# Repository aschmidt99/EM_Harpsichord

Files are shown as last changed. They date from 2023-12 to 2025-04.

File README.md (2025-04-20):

# NOTE: This repo is outdated!
Hello! While this repository still covers the basics of Lorentz Force Actuation and feedback, a more comprehensive and curated version can be found on this newer repository: [Sparksichord Project](https://github.com/aschmidt99/Sparksichord_NIME2025)

# Electromagnetic Harpsichord

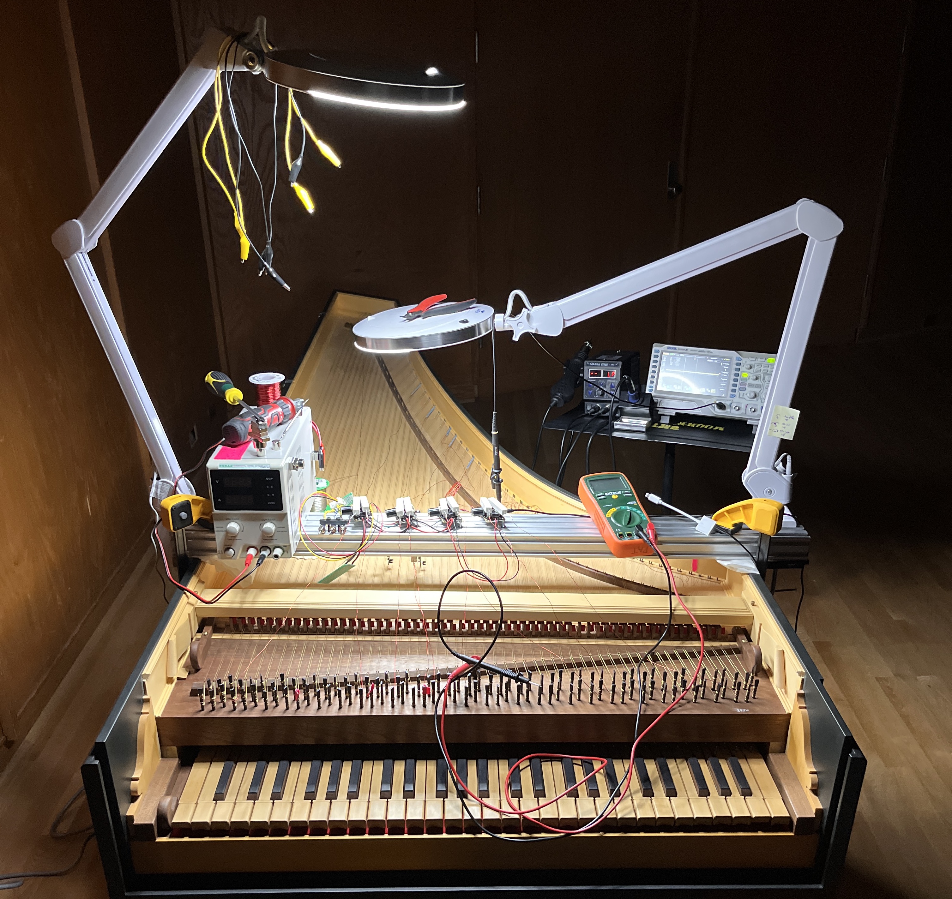
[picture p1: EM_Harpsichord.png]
EM_Harpsichord


The EM Harpsichord is an augmented harpsichord that uses optical sensors, audio power amplifier chips, and some simple signal processing to sustain the vibrations of its brass strings. This early prototype uses one circuit board for every string you wish to sustain. A work-in-progress performance/demonstration was given on October 2nd, 2023 at the 63rd Annual University of Michigan Organ Conference. For this demonstration, 3 strings had optical sustaining enabled and 8 strings had audio-playback enabled.

## Video Examples
Here is a [selection of audio examples](https://drive.google.com/drive/folders/1B2c4qz-7Rl1Y2wPH64m0Ud0_MTGL74a2?usp=sharing) of both sustainers and audio playback through the harpsichord strings.

## Working Principle
This simple board uses a ITR20403 Optical Photo-interrupt to sense the vibrations (position) of a harpsichord string. The derivative of this signal is amplified and sent to a 5-Watt audio amplifier chip (PAM8406) that is normally used to power small 4 or 8 ohm speakers. Rather than connect to a speaker, the output terminals of the speaker chip are connected to each end of one of the strings on a harpsichord. The amplified signal pushes current through the string, which generates an alternating magnetic field that interacts with a strong magnetic field from permanent neodymium magnets.

The working principle is similar to the more familiar eBow, but rather sensing and inducing vibrations with electromagnetic coils, we sense with an optical sensor and actuate with Lorentz force actuation.

## Simple System Diagram
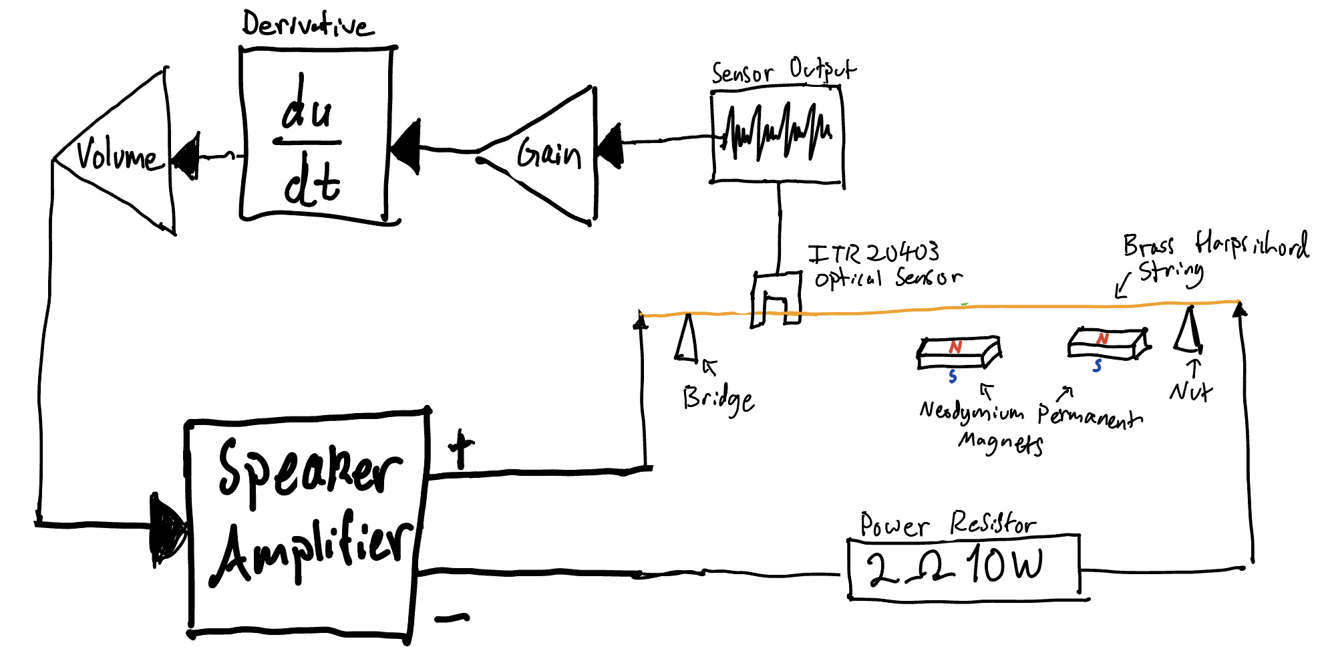
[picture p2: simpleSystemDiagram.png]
simpleSystemDiagram

This is the signal flow for the sustainer circuit in each board. You need one circuit board for each string you wish to sustain.

## The Circuit Board
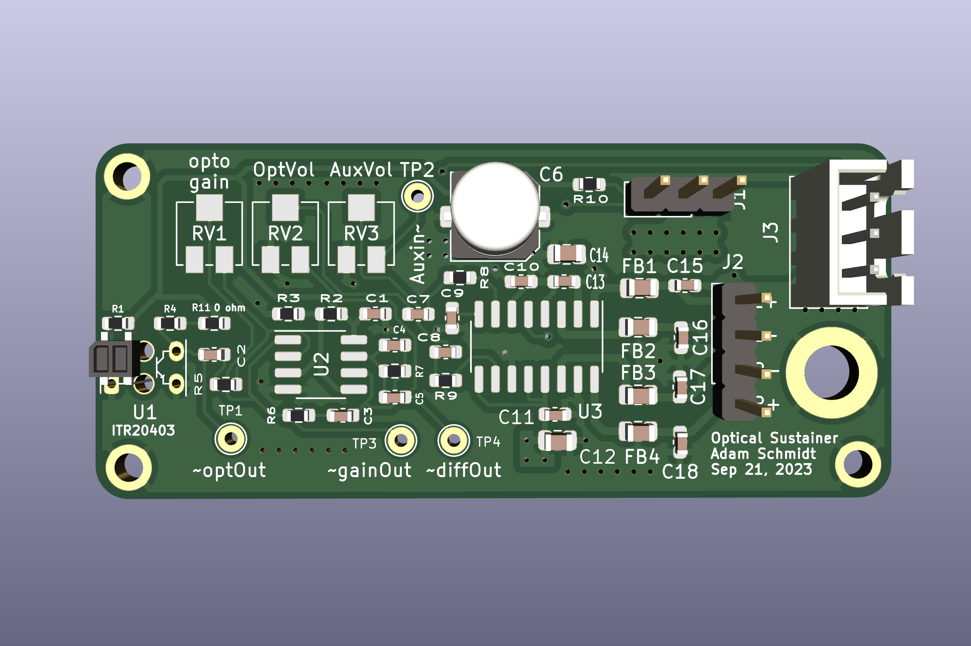
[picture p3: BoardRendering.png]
PCB

The circuitboard is thin enough to fit between the harpsichord's strings. We mounted them to an aluminum extrusion C Beam with slide nuts, M4 screws, and some small 3D printed brackets.

## How to order
### JLCPCB
If you wish to have this exact board, you can order these circuit boards from JLCPCB by uploading GERBER-EMHarpsichord_Sustainer+Playback.zip to JLCPCB. Also upload BOM-EMHarpsichord_Sustainer+Playback.csv and CPL-EMHarpsichord_Sustainer+Playback.csv to have JLCPCB assemble the board for you.
(Note: Double check the orientation of each IC in JLCPCB. They are often incorrect by default.)

### Reach out to me
Alternatively, reach out to me (schmia@umich.edu) in case I have some extra :)

### Other board house
If you are familiar with a different board house, feel free to export as you usually would from KiCad.

### Notes before ordering/assembling
If you order based on my files, the optical sensor will be placed on the wrong side of the board. I found it easier to source the components from JLCPCB and desolder/resolder the ITR20403 to the other side of the board. If you can find them for cheap elsewhere, it would probably save you a small headache to order them separately and omit them from the board when ordering.

## How to use
### Wiring up
- A 3 Pin JST XH 2.54mm connector supplies 5V, Ground, and an auxiliary audio input. If you don't anticipate using audio playback, simply wire up the 5V and Ground and you are good to go. Chain several boards together to sustain multiple notes. We put a SPST switch between each board's ground and the power supply ground to allow us to select which strings were activated individually.
- The PAM8406 chip is advertised to support 4-8 ohm loads, though the data sheet notes that it can support loads down to 2 ohms. The data sheet also notes that outputs of the PAM8406 amplifier chip have built in short circuit protection, and the outputs will not activate if they detect less than 2 ohm load. Therefore, you must ensure that there are at least 2 ohms between the (+) and (-) terminal of each speaker output.
	- Most of the brass strings on our harpsichord measured much less than 1 Ohm, so we opted to put a 2-Ohm 10W Power Resistor between each string and one of the terminals the selected channels.

### Magnets
- To induce vibration, the strings must be exposed to a strong magnetic field. We have been using N52 neodymium magnets (purchased from kjmagnetics.com) for this purpose. The strength of the vibration is proportional to the strength of the magnetic field, and although the presence of just one or two magnets usually is enough to get sound going, more magnets seems to encourage a higher acoustic output.
- The orientation of the magnet does matter. Flip the magnet back and forth to determine which side is inducing the sound you like. One side should sustain the fundamental frequency of the string and the other may damp the fundamental while favoring odd harmonics.
- If you wish to use multiple magnets on a string, you will most likely want all of their poles pointed in the same direction, although interesting magnet placement can yield interesting results...

### Channels
- The 'left' output channel of the board is connected to the optical sensor, which creates a closed feedback loop to sustain vibrations on the connected string.
- The 'right' output channel of the board amplifies an auxiliary input signal.

### Additional Notes:
- The optical sensor needs to be placed very precisely over the string to ensure it picks up the vibration. The sensing range of the string is very small and is easy to clip. You can use an oscilloscope on test point 1 (TP1) to make sure the sensor isn't clipping before the gain stage.
- If it is clipping (and you do not like the output tone), consider moving the sensor board closer to a termination point of the string where its range of vibration is much smaller. This should yield a smoother sustaining sound.
- The feedback loop is very sensitive to the position of the sensor. You will likely notice timbral changes as you change the point on the string where the sensor is located, the position of the sensor over the string, and the positions of the magnets.
- Bar magnets induce stronger vibrations than cylindrical with the same pull force.
- The resistance of a metal string is a function of its material, gauge, length, and temperature. The higher the resistance, the more apt the string is to detuning. If your strings are detuning too much, try using a thicker wire, more conductive material, or lower current. If you are building a new instrument rather than augmenting an existing one, try different string lengths.

## Design References
- the 'RelevantDocuments' folder holds data sheets and some blog/forum posts I found helpful while designing the board. (Dave Corsie's blog)[https://www.davecorsie.com/optical-pickup-blog] helped me figure out how to design the optical pickup circuit and the DIYAudio blog helped me make a better PCB layout for the PAM8406 Chip.

## Future Improvements
### Support Loads < 2 Ohms
One of the most obvious shortcomings of this system is the wasted power. If a given string is only 0.2 Ohms and we compensate with a 2 Ohm resistor, most (~90%) of the power is being dissipated as heat through the resistor rather that contributing towards generating vibrations. I suspect looking into circuits that are anticipating extremely low loads such as ribbon speaker amplifiers will be a worthwhile endeavor and likely be a solution for the next version of this circuit.

### Lower Heat Buildup
On the other hand, the large dummy load ensures the majority of the power is dissipated somewhere other than the string, which prevents heat buildup (and thus detuning) in the string. The magnetic field generated by the string is proportional to current only - it does not factor in voltage. Therefore, an alternative system improvement may be to increase string gauges to /decrease/ overall resistance and continue to utilize the power resistors.

### Controlled Detuning
With more advanced feedback control, it may be possible to control how much or little each string is detuned during actuation. This could allow the performer to change tuning systems rapidly and on-the-fly - a process that usually takes considerable time and attention.

### Sustainer on every string
A natural progression for the project is to add a sustainer board for every string so that we can sustain any strings rather than just the few we chose for our work-in-progress demonstration. A double-manual harpsichord might work well, where one manual controls the sustainers and the other moves jacks and plucks the strings as usual.

### Sensing the keys
In the next version of this project, we aim to actively sense the position of each harpsichord key to use as a control signal for the sustainer of each corresponding string. Mechanically separating the harpsichord keys from the strings will allow us to map and re-map the interaction between key presses and actuation however we wish.

## Acknowledgements
- This project was enabled by Professor Joseph Gascho, Associate Professor of Music and Director of the Stearns Collection at the University of Michigan Ann Arbor.
- This project was inspired by the (Electromagnetic Resonator Piano)[http://instrumentslab.org/research/mrp.html], a project by Andrew McPherson at the Augmented Instruments Lab.
- Additional inspiration and insight was provided by (Techniques and Circuits for Electromagnetic Instrument Actuation)[https://www.nime.org/proceedings/2012/nime2012_117.pdf] by Andrew McPherson (see Section 2.4 - Lorentz Force Sustaining).

## Software Versions used
- KiCad (6.0.7-1)-1 for MaxOS Version 13.4.1
- LTSpice 17.0.40 for OS X

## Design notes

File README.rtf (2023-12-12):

# Electromagnetic Harpsichord

The EM Harpsichord is an augmented harpsichord that uses optical sensors, audio power amplifier chips, and some simple signal processing to sustain vibrations on the brass strings of the harpsichord. This early version uses one circuit board per string you wish to sustain. A work-in-progress performance/demonstration was given on October 2th, 2023 at the 63rd Annual University of Michigan Organ Conference.

## Working Principle

This simple board uses a ITR20403 Optical Photo-interrupt to sense the vibrations (position) of a harpsichord string. The derivative of this signal is amplified and sent to a 5-Watt audio amplifier chip (PAM8406) that is normally connected to small 4 or 8 ohm speakers. Rather than connect to a speaker, the output terminals of the speaker chip are connected to each end of one of the strings on a harpsichord. The amplified signal pushes

## How to order:

You can order these circuit boards by uploading GERBER-EMHarpsichord_Sustainer+Playback.zip to JLCPCB. Additionally upload BOM-EMHarpsichord_Sustainer+Playback.csv and CPL-EMHarpsichord_Sustainer+Playback.csv to have JLCPCB assemble the board for you.
- Double check the orientation of each IC in JLCPCB. They are often incorrect by default.

Alternatively, reach out to me (schmia@umich.edu) in case I have some laying around still :)

## How to use:

### Wiring up

- The PAM8406 chip is advertised to support 4-8 ohm loads, though the data sheet notes that it can support loads down to 2 ohms. The data sheet also notes that outputs of the PAM8406 amplifier chip have built in short circuit protection, and the outputs will not activate if they detect less than 2 ohm load. Therefore, you must ensure that there are at least 2 ohms between the (+) and (-) terminal of each speaker output. Most of the brass strings on our harpsichord measured less than 1 Ohm (a function, so we opted to put a 2-Ohm 10W Power Resistor between each string and one of the terminals the selected channels.

### Magnets

- To induce vibration, the strings must be exposed to a strong magnetic field. We have been using strong neodymium magnets (purchased from kjmagnetics.com) for this purpose. The strength of the vibration is proportional to the strength of the magnetic field, and although the presence of just one or two magnets usually seems to be enough,

- The left output channel of the board to the optical sensor which creates a closed feedback loop to sustain vibrations on the connected string.

Additional Notes:
- The optical sensor needs to be placed very precisely over the string to ensure it picks up the vibration. The sensing range of the string is very small and is easy to clip. You can use an oscilloscope on test point 1 (TP1) to make sure the sensor isn’t clipping before the gain stage.
- If it is clipping, consider moving the sensor board closer to a termination point of the string where its range of vibration is much smaller.
- The feedback loop is very sensitive to the position of the sensor. You will likely notice timbral changes as you change the point on the string where the sensor is located, the position of the sensor over the string, and the positions of the magnets.
- Bar magnets seem to work better than cylindrical with the same pull force.

- The right output channel of the board amplifies an auxiliary input signal (from

### Notes before ordering/assembling

- the optical sensor will be placed on the wrong side of the board, but I found it easier to source the components from JLCPCB and desolder/resolder the ITR20403 to the other side of the board. If you can find them for cheap elsewhere, it would probably save you a small headache to order them separaetly and omit them from the board.

## Design Notes

- the RelevantDocuments folder holds data sheets and some blog/forum posts I found helpful while designing the board. Dave Corsie’s blog helped me figure out how to design the optical pickup circuit and the DIYAudio blog helped me make a better PCB layout for the PAM8406 Chip

## Future Improvements

## Software Versions

KiCad (6.0.7-1)-1 for MaxOS Version 13.4.1
LTSpice 17.0.40 for OS X

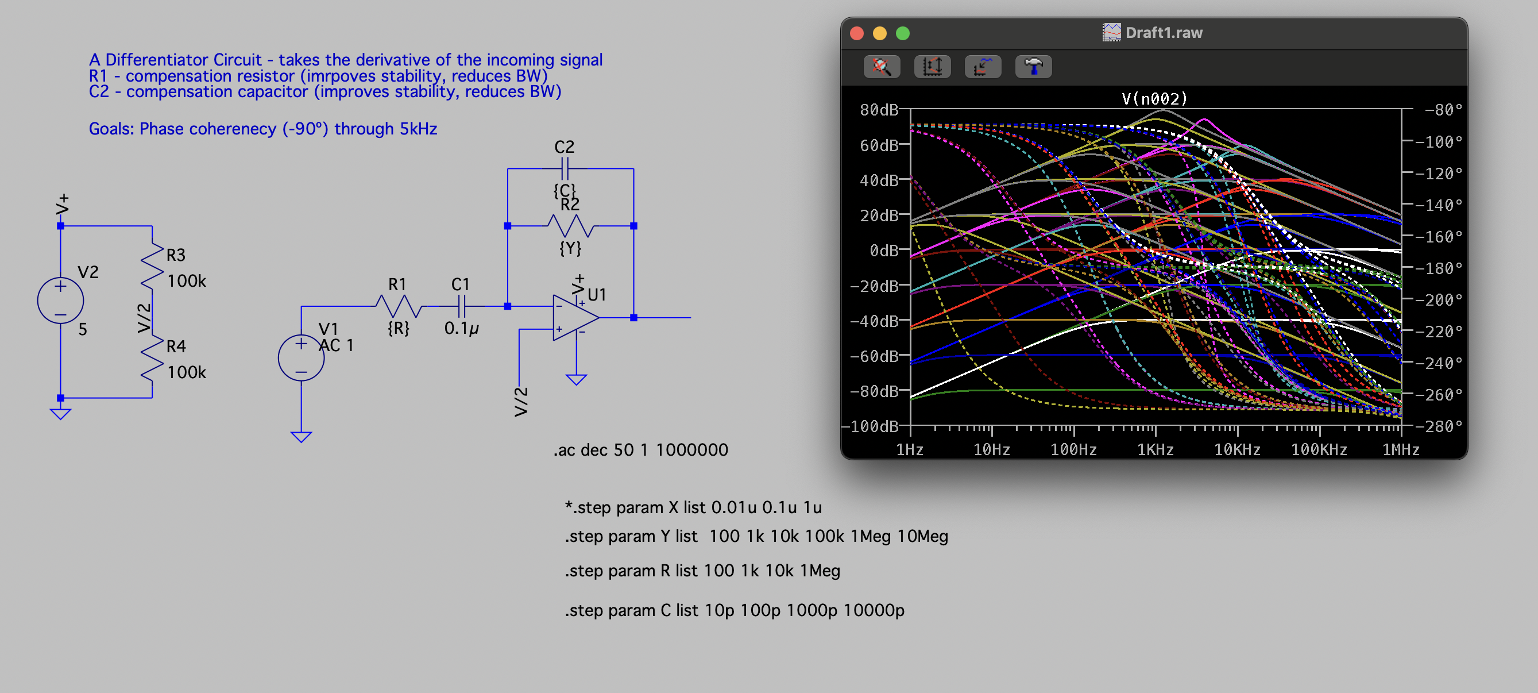
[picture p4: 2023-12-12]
Electronics/ProgressScreenshots/Differentiator_finding_values.png

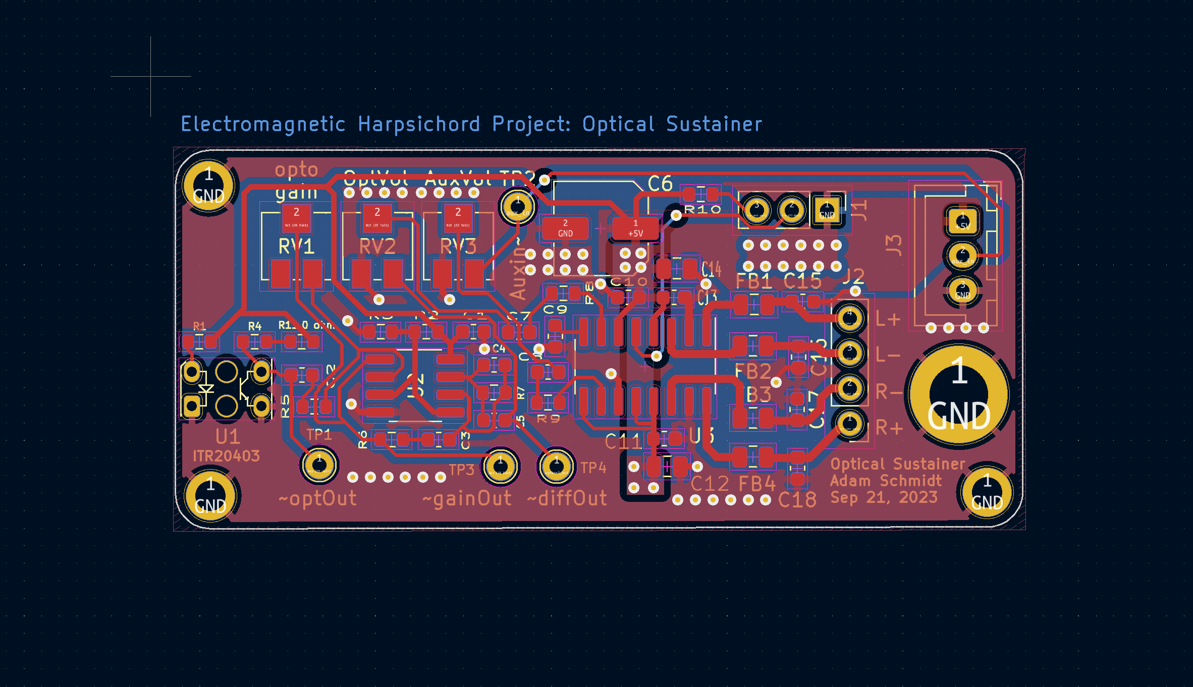
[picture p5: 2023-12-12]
Electronics/ProgressScreenshots/BoardLayers_Sep21_2023.png

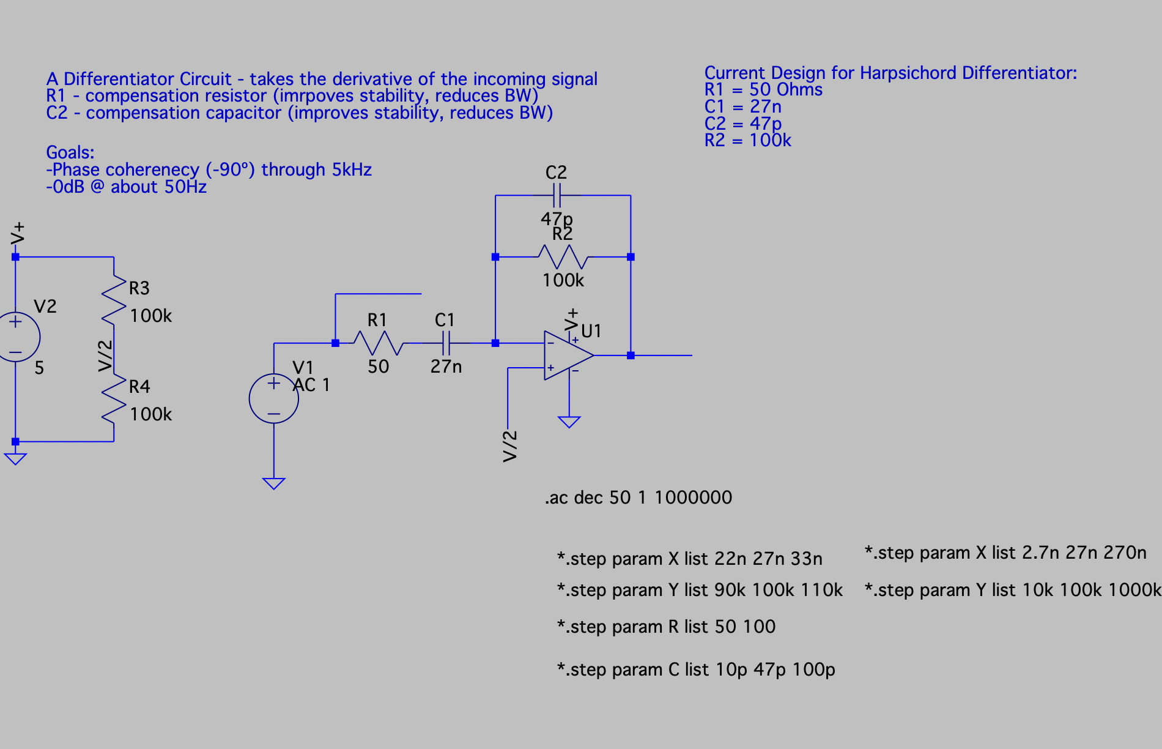
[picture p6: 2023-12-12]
Electronics/ProgressScreenshots/Differentiator_final_values.png

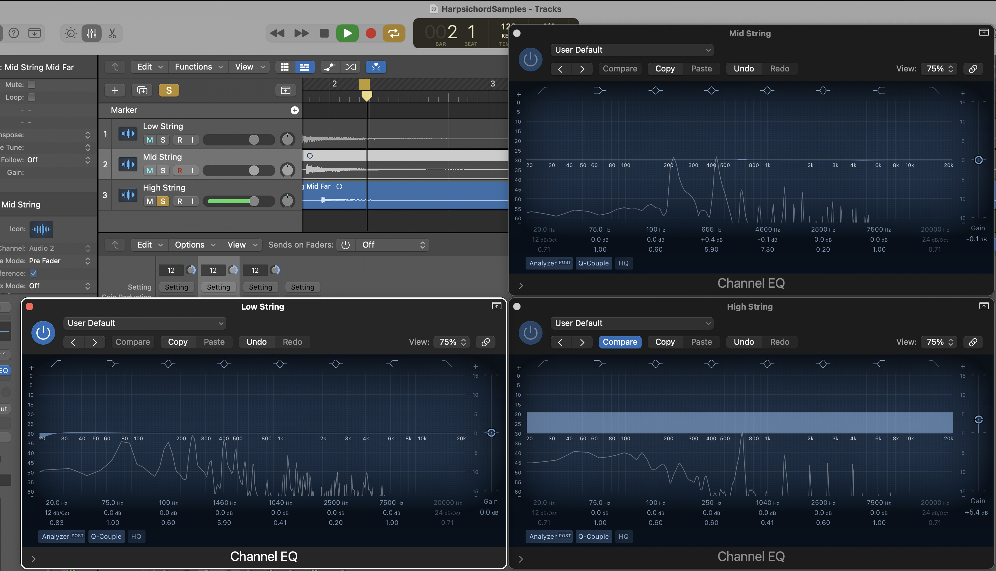
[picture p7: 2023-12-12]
Images/FindingHarmonicProfileOfHarpsichord2.png

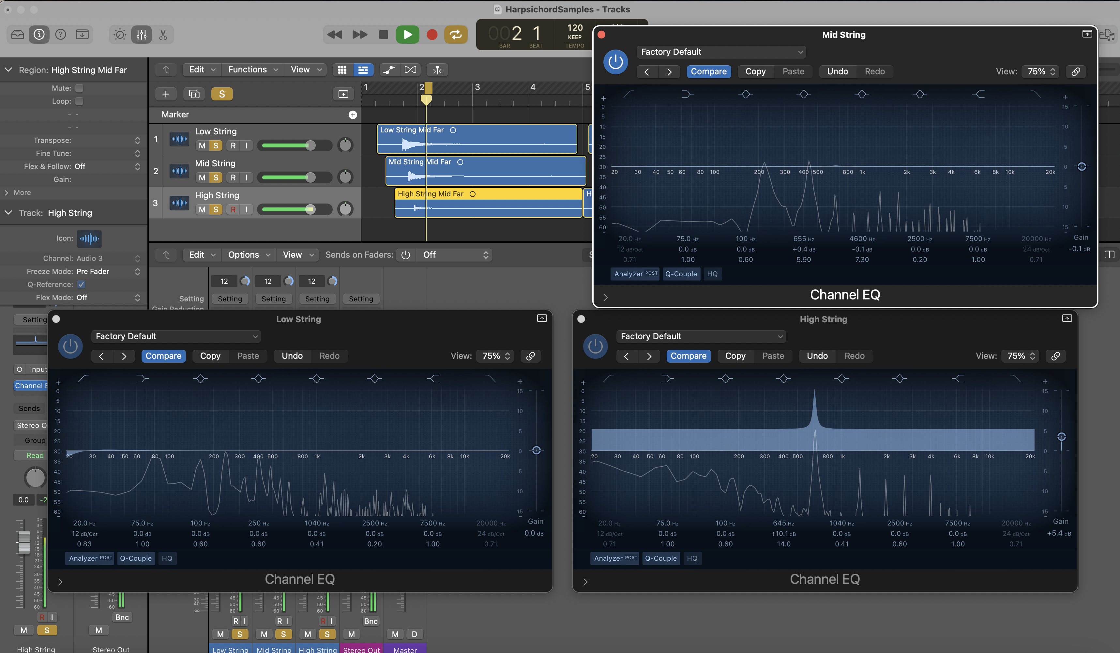
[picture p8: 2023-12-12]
Images/FindingHarmonicProfileOfHarpsichord.png

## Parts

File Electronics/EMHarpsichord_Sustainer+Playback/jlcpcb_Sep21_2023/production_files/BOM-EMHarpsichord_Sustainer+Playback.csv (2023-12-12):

Comment | Designator | Footprint | LCSC
Conn_01x03_Male | J3 | JST_XH_B3B-XH-A_1x03_P2.50mm_Vertical | C161870
220u | C6 | C_Elec_6.3x5.8 | C497579
ITR20403 | U1 | Everlight_ITR20403 | C5135
20k | RV2 | Potentiometer_Bourns_3224J_Horizontal | C719181
100k | RV1,RV3 | Potentiometer_Bourns_3224J_Horizontal | C719185
NE5532 | U2 | SOP-8_3.76x4.96mm_P1.27mm | C7426
PAM8406D | U3 | SOP-16_3.9x9.9mm_P1.27mm | C86270
opt_out | TP4 | TestPoint_THTPad_D2.0mm_Drill1.0mm
2.2u | C2 | C_0603_1608Metric
20k | R4 | R_0603_1608Metric
0 | R11 | R_0603_1608Metric
Conn_01x04_Male | J2 | PinHeader_1x04_P2.54mm_Vertical
5A/120Ohm | FB3 | C_0805_2012Metric
22n | C3 | C_0603_1608Metric
PT_out | TP1 | TestPoint_THTPad_D2.0mm_Drill1.0mm
220p | C17 | C_0603_1608Metric
Conn_01x03_Male | J1 | PinHeader_1x03_P2.54mm_Vertical
10k | R2 | R_0603_1608Metric
10k | R10 | R_0603_1608Metric
1u | C7 | C_0603_1608Metric
2.2u | C5 | C_0603_1608Metric
gain_out | TP3 | TestPoint_THTPad_D2.0mm_Drill1.0mm
5A/120Ohm | FB4 | C_0805_2012Metric
10k | R5 | R_0603_1608Metric
1u | C9 | C_0603_1608Metric
1k | R6 | R_0603_1608Metric
220p | C18 | C_0603_1608Metric
1u | C11 | C_0603_1608Metric
220p | C15 | C_0603_1608Metric
1u | C13 | C_0603_1608Metric
100n | C1 | C_0603_1608Metric
220p | C16 | C_0603_1608Metric
1u | C10 | C_0603_1608Metric
220 | R1 | R_0603_1608Metric
1u | C8 | C_0603_1608Metric
5A/120Ohm | FB1 | C_0805_2012Metric
10u | C12 | C_0805_2012Metric
10k | R3 | R_0603_1608Metric
100k | R7 | R_0603_1608Metric
10u | C14 | C_0805_2012Metric
MountingHole | TP6 | TestPoint_THTPad_D2.0mm_Drill1.0mm
5A/120Ohm | FB2 | C_0805_2012Metric
10k | R8 | R_0603_1608Metric
10k | R9 | R_0603_1608Metric
aux_in | TP2 | TestPoint_THTPad_D2.0mm_Drill1.0mm
47p | C4 | C_0603_1608Metric

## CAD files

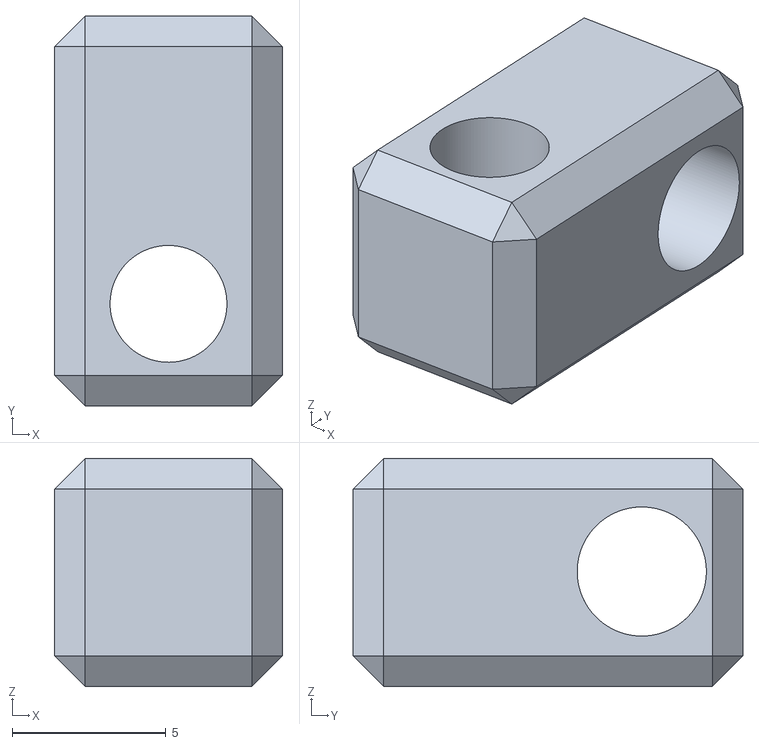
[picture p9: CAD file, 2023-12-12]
CAD/Link1.stl
7.42 x 12.7 x 7.42

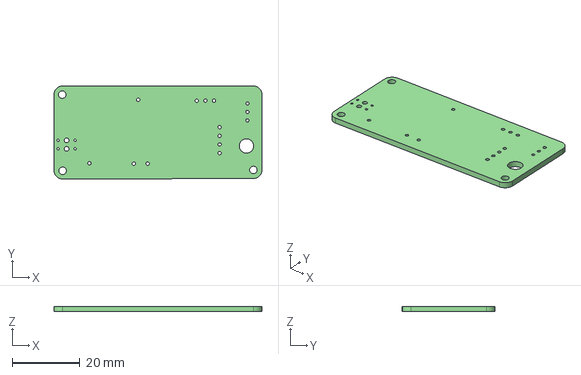
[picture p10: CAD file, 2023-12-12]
Electronics/EMHarpsichord_Sustainer+Playback/EMHarpsichord_Sustainer+Playback.step
61.2 x 27.4 x 1.60 mm

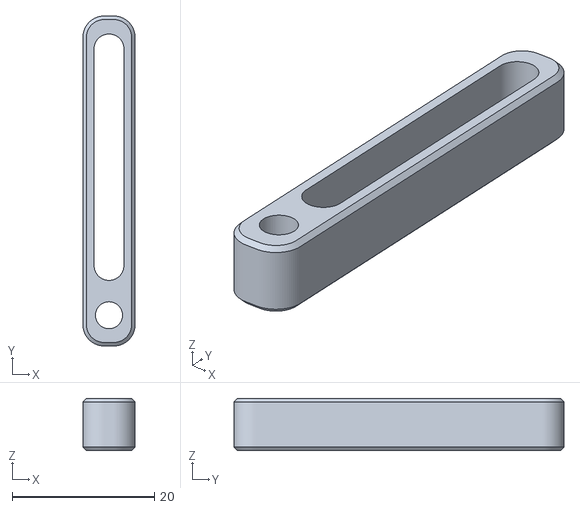
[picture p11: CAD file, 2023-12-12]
CAD/Link2.stl
7.34 x 46.4 x 7.34

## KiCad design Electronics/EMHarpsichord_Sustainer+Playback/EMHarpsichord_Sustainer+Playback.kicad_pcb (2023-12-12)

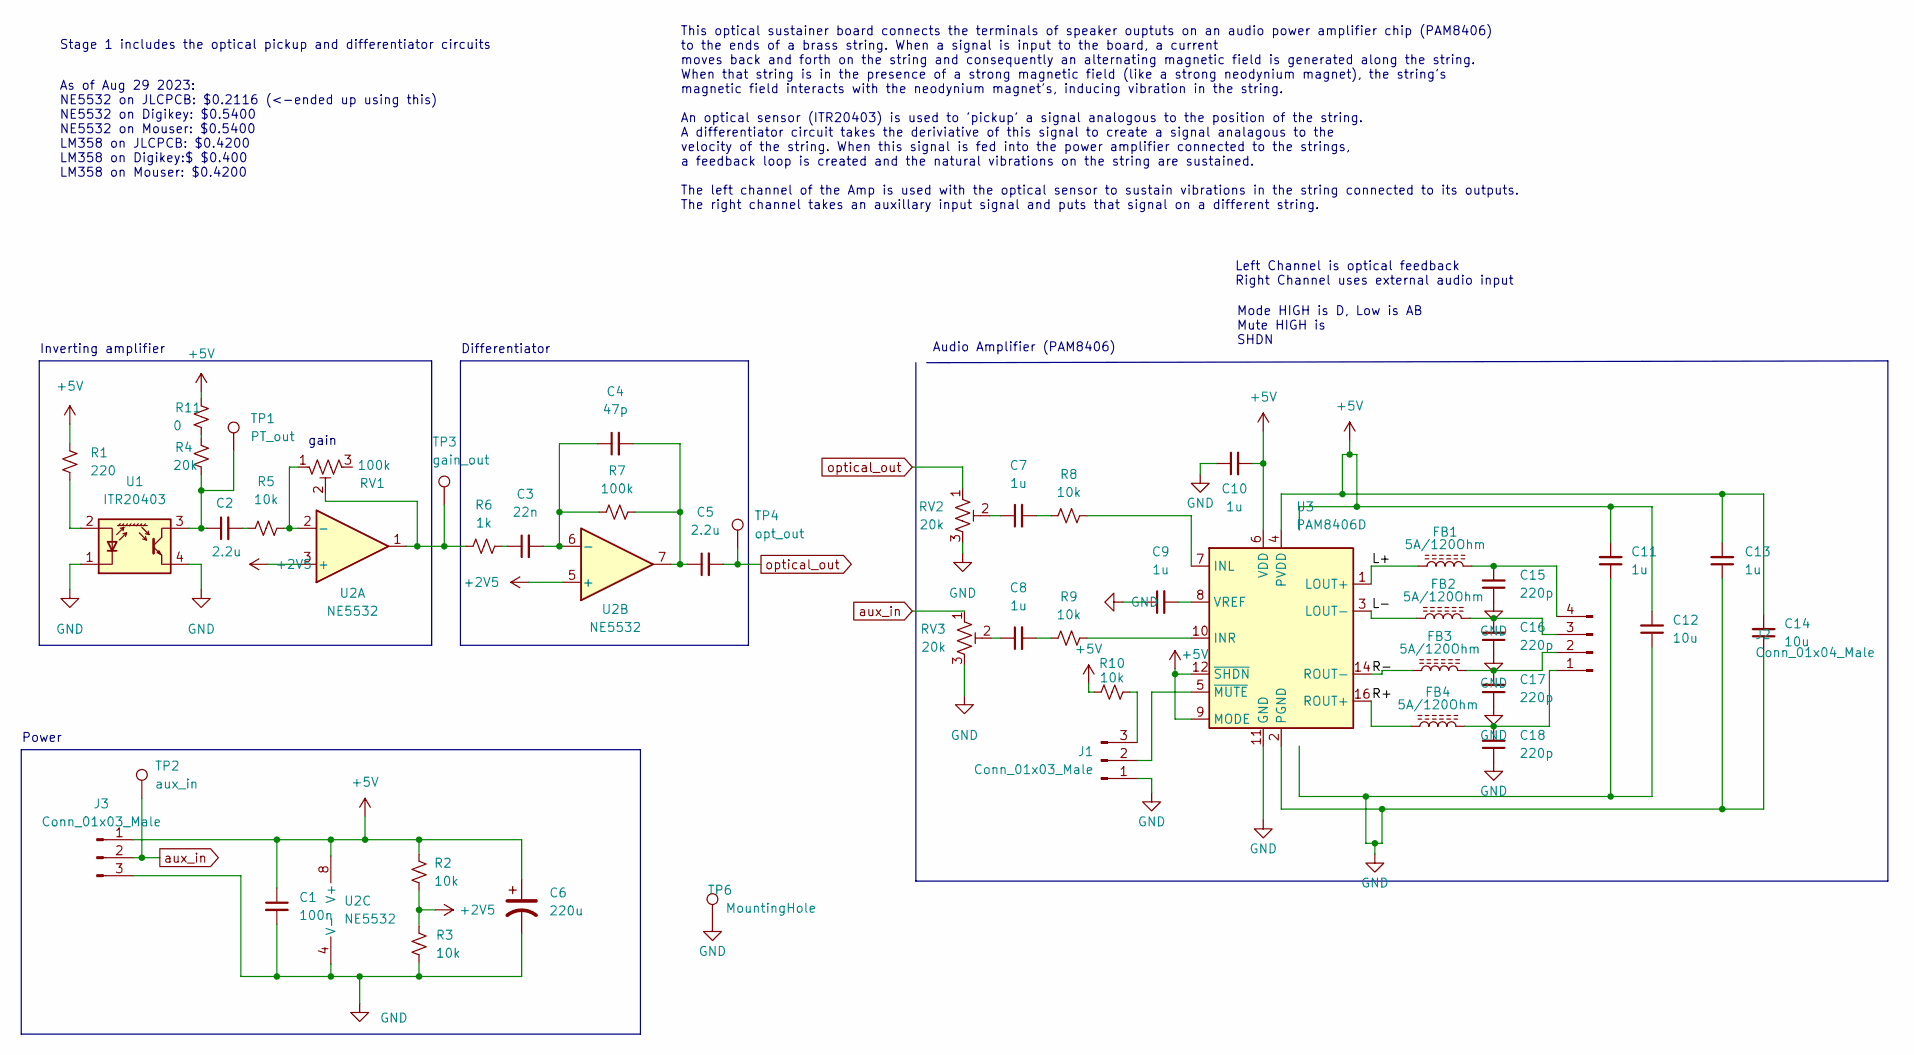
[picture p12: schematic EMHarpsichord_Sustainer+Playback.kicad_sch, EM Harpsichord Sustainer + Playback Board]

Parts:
C1: 100n; C_0603_1608Metric
C2, C5: 2.2u; C_0603_1608Metric
C3: 22n; C_0603_1608Metric
C4: 47p; C_0603_1608Metric
C6: 220u; C_Elec_6.3x5.8; LCSC C497579
C7, C8, C9, C10, C11, C13: 1u; C_0603_1608Metric; Rating 10V
C12, C14: 10u; C_0805_2012Metric; Rating 10V
C15, C16, C17, C18: 220p; C_0603_1608Metric; Rating 10V
FB1, FB2, FB3, FB4: 5A/120Ohm; C_0805_2012Metric; LCSC C304323
J1: Conn_01x03_Male; PinHeader_1x03_P2.54mm_Vertical; LCSC C2914353
J2: Conn_01x04_Male; PinHeader_1x04_P2.54mm_Vertical
J3: Conn_01x03_Male; JST_XH_B3B-XH-A_1x03_P2.50mm_Vertical; LCSC C161870
R1: 220; R_0603_1608Metric
R2, R3, R5, R8, R9, R10: 10k; R_0603_1608Metric
R4: 20k; R_0603_1608Metric
R6: 1k; R_0603_1608Metric
R7: 100k; R_0603_1608Metric
R11: 0; R_0603_1608Metric
RV1: 100k; Potentiometer_Bourns_3224J_Horizontal; LCSC C719185
RV2: 20k; Potentiometer_Bourns_3224J_Horizontal; LCSC C719181
RV3: 20k; Potentiometer_Bourns_3224J_Horizontal; LCSC C719185
TP1: PT_out; TestPoint_THTPad_D2.0mm_Drill1.0mm
TP2: aux_in; TestPoint_THTPad_D2.0mm_Drill1.0mm
TP3: gain_out; TestPoint_THTPad_D2.0mm_Drill1.0mm
TP4: opt_out; TestPoint_THTPad_D2.0mm_Drill1.0mm
TP6: MountingHole; TestPoint_THTPad_D2.0mm_Drill1.0mm
U1: ITR20403; Everlight_ITR20403; LCSC C5135
U2: NE5532; SOP-8_3.76x4.96mm_P1.27mm; LCSC C7426
U3: PAM8406D; SOP-16_3.9x9.9mm_P1.27mm; LCSC C86270

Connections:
+2V5: R2.1, R3.2, U2.3 (+), U2.5 (+)
+5V: C1.1, C6.1, C10.2, C11.2, C12.2, C13.2, C14.2, J3.1, R1.1, R2.2, R10.1, R11.1, U2.8 (V+), U3.4 (PVDD), U3.6 (VDD), U3.9 (MODE), U3.12 (~SHDN), U3.13 (PVDD)
/L+: FB1.1, U3.1 (LOUT+)
/L-: FB2.1, U3.3 (LOUT-)
/R+: FB4.1, U3.16 (ROUT+)
/R-: FB3.1, U3.14 (ROUT-)
GND: C1.2, C6.2, C9.1, C10.1, C11.1, C12.1, C13.1, C14.1, C15.1, C16.1, C17.1, C18.1, J1.1, J3.3, R3.1, RV2.3, RV3.3, TP6.1, U1.1 (K), U1.4 (E), U2.4 (V-), U3.2 (PGND), U3.11 (GND), U3.15 (PGND)
unnamed: C2.1, R4.2, TP1.1, U1.3 (C)
unnamed: C2.2, R5.1
unnamed: C3.1, R6.2
unnamed: C3.2, C4.1, R7.1, U2.6 (-)
unnamed: C4.2, C5.1, R7.2, U2.7
unnamed: C7.1, RV2.2
unnamed: C7.2, R8.1
unnamed: C8.1, RV3.2
unnamed: C8.2, R9.1
unnamed: C9.2, U3.8 (VREF)
unnamed: C15.2, FB1.2, J2.4
unnamed: C16.2, FB2.2, J2.3
unnamed: C17.2, FB3.2, J2.2
unnamed: C18.2, FB4.2, J2.1
unnamed: R1.2, U1.2 (A)
unnamed: R5.2, RV1.1, U2.2 (-)
unnamed: R6.1, RV1.2, TP3.1, U2.1
unnamed: R8.2, U3.7 (INL)
unnamed: R9.2, U3.10 (INR)
unnamed: J1.3, R10.2
unnamed: R4.1, R11.2
unnamed: J1.2, U3.5 (~MUTE)
aux_in: J3.2, RV3.1, TP2.1
optical_out: C5.2, RV2.1, TP4.1

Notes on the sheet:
Left Channel is optical feedback Right Channel uses external audio input
Power
This optical sustainer board connects the terminals of speaker ouptuts on an audio power amplifier chip (PAM8406) to the ends of a brass string. When a signal is input to the board, a current moves back and forth on the string and consequently an alternating magnetic field is generated along the st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
Audio Amplifier (PAM8406)
Mode HIGH is D, Low is AB Mute HIGH is SHDN
Differentiator
As of Aug 29 2023: NE5532 on JLCPCB: $0.2116 (<-ended up using this) NE5532 on Digikey: $0.5400 NE5532 on Mouser: $0.5400 LM358 on JLCPCB: $0.4200 LM358 on Digikey:$ $0.400 LM358 on Mouser: $0.4200
Inverting amplifier
gain
Stage 1 includes the optical pickup and differentiator circuits

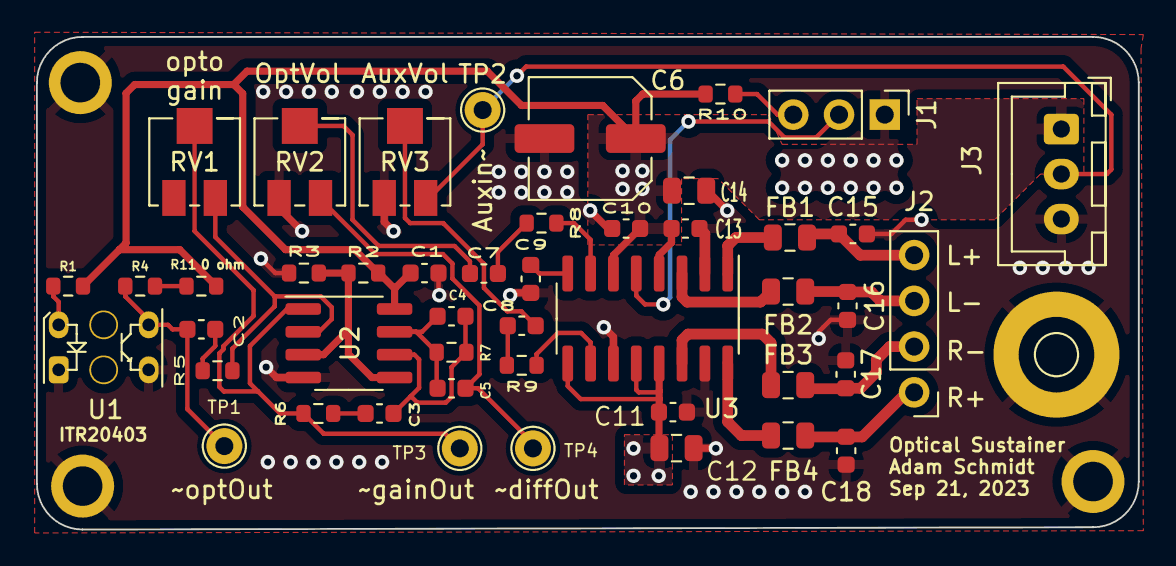
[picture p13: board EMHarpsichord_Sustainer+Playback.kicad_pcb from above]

Board: 2 copper layers, 61.2 x 27.4 mm, 47 parts (0 on the bottom side), 31 nets.

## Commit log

2023-12-12 initial commit to github
    Organizing EM Harpsichord files:
    On github: CAD, Code, Electronics, some images
    offline: receipts, most audio files, videos
    [BOM-EMHarpsichord_Stage1.csv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]
2023-12-12 Reorganizing and Naming files
    [BOM-EMHarpsichord_Stage1.csv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]
2023-12-12 More tidying files and adding comments to schematics
    [EMHarpsichord_Sustainer+Playback.kicad_pcb, EMHarpsichord_Sustainer+Playback.kicad_sch]
2023-12-12 updating the readme
    also renamed some files
    [BOM-EMHarpsichord_Sustainer+Playback.csv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]
2025-04-20 Linking Updated Repo: Sparksichord_NIME2025
    This is now an outdated project and has been replaced by the following repo: https://github.com/aschmidt99/Sparksichord_NIME2025
    [EMHarpsichord_Sustainer+Playback.kicad_sch]
